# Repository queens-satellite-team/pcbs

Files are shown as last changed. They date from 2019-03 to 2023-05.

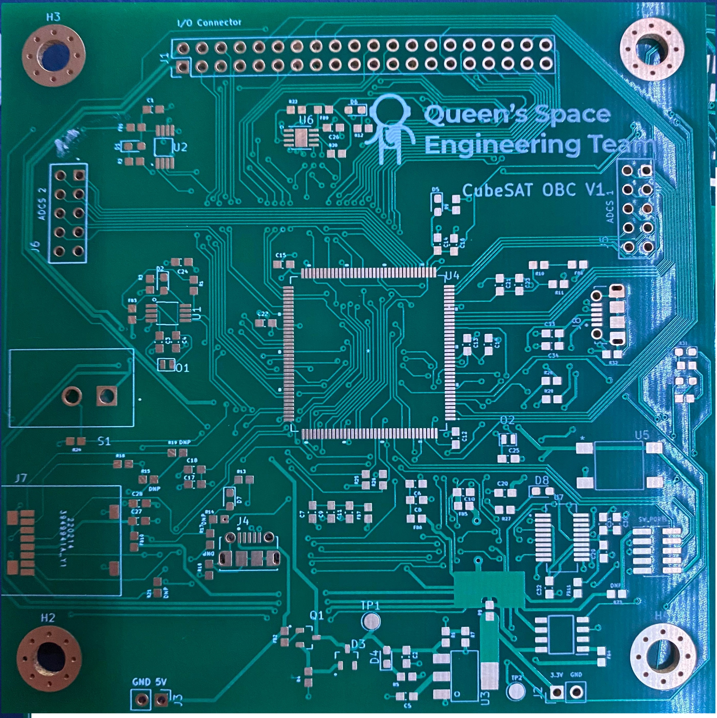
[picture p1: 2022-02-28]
OBC_Boards/STM32_Breakout/PCB_Frontside.jpg

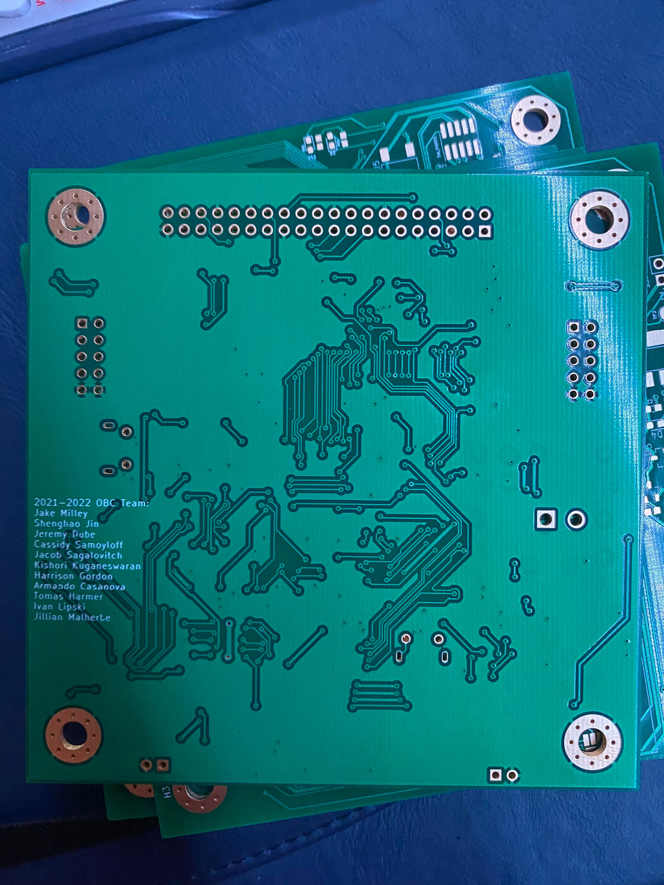
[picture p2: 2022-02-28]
OBC_Boards/STM32_Breakout/PCB_Backside.jpg

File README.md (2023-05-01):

# QSAT PCB Files

## Overview
This README contains information on how to setup your KiCad 6.0 environment. It includes:
1. How to use the existing schematic symbols and layout footprints
2. How to start a new project from an existing template
3. How to prepare the manufacturing and assembly files for ordering from JLCPCB

## Using QSAT PCB Symbols and Footprints

Following the instructions provided here: [How to Import into KiCad v6](https://support.snapeda.com/en/articles/5995733-how-to-import-into-kicad-v6-later)

**Import Symbols**

1. In KiCad, go to Preferences.

2. Click on Manage Symbol Libraries.

3. On the Global Libraries tab, click on Browse Libraries (the small folder icon below) 

4. Select the .lib file, then click Open. 

5. The library will appear, click OK.

6. Click on Symbol Editor.

7. Type on the filter search field, and navigate to the symbol you imported. Double-click over it to open the file.

**Import Footprints**

Using the *.kicad_mod file:

1. In KiCad, go to Preferences.

2. Click on Manage Footprint Libraries.

3. On the Global Libraries tab, click on Browse Libraries (the small folder icon below) 

4. Navigate to the Folder of the downloaded .kicad_mod file. Then click Select Folder. 

5. The library will appear, click OK. 

6. Click on Footprint Editor.

7. Type on the filter search field, and navigate to the footprint you imported. Double-click over it to open the file.

## Using QSAT PCB Templates

Following the instructions provided here: [KiCad Creating Templates](https://docs.kicad.org/5.1/en/kicad/kicad.html#creating_templates) we must:

1. Update our path configurations in KiCad to include the template folder.

a. Go to *Preferences* -> *Configure Paths* in the KiCad GUI.

b. Go to *KICAD_USER_TEMPLATE_DIR* and double click the path name until a folder apprears. 

c. Navigate to the *QSAT/pcbs/qsat-templates* directory and hit *Select Folder*

2. Create a new project from the template. 

a. Go to *File* -> *New Project From Template...* in the KiCad GUI.

b. Select the *User Templates* tab, and choose the template you want. 

**Note:** If starting a project from scratch it is recommended to use the *QSAT - PC104 Base Board* 
This is designed to have the same pcb footprint as the Clyde Space EPS board with mounting holes and
a PC104 connector.

## Ordering From JLCPCB

JLC has provided instructions for their required procedure, and is well detailed. 

The steps to generate the manufacturing files are found [here](https://support.jlcpcb.com/article/194-how-to-generate-gerber-and-drill-files-in-kicad-6). 

And the steps to generate the BOM and Centroid files are found [here](https://support.jlcpcb.com/article/84-how-to-generate-the-bom-and-centroid-file-from-kicad).

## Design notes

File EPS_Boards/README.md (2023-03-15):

EPS Printed Circuit Boards

**Note:** For the Solar Panel RevA, this file was made in KiCad 7.0 and can not be opened with earlier KiCad versions. 

|Board Name|Description|Status|Dinosaur Nickname|
|-|-|-|-|
|Solar Panel RevA| Supplies power generation capabilities for the satellite. Current PCB design is a smaller ~1U version to be used for testing. | Fabricated | TBD |
|Battery Board| Supplies power storage capabilites for the satellite. Contains voltage and current protections at the cell and system level. | In Progress | TBD |

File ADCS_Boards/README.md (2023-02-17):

# ADCS PCB Boards CSDC-6 (2022-2023)
We have three PCBs for ADCS. Their functionality is described below.

|Board Name|Description|Status|Dinosaur Nickname|
|-|-|-|-|
|Controller Board|The controller board houses the MCU and associated circuits, as well as the sun sensors.|In Progress|Irritator|
|Reaction Wheel Board|The RW-BD contains the reaction wheel driver boards and the IMUs.|In progress|Brachiosaurus|
|Magnetorquer Board|The MTQ-BD houses the magnetorquer coils and associated circuitry. If dedicated magnetometers are needed, they may be added to this board.|In Progress|Magyarosaurous|
|Photodiode Breakout Board|The photodiode board houses the photodiodes and is mounted to the solar panel boards|Completed|Ankylosaurus|

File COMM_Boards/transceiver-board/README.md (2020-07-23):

# QSAT transceiver-board 
This is the repo for the design of the tranciever for QSET's cube sattelite over 2018-2020
This may be made into a wiki, for now the readme works 

The following is a list of what is where: 

## Docs 
This folder contains the docs for the tranciver board meaning notes, and data sheets 
This is where the bill of materials and needs also live 
## Layout 
This has the KiCAD files for the tranciver layout

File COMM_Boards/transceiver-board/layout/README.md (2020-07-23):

# QSAT Tranciever Layout 
This part of the repo contains all of the KiCAD models 
Each version of the board is stored in a seperate folder with a version number

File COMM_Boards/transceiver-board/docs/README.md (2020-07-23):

# QSAT Tranceiver Document Storage 
This folder contains all documation and design notes, below is a listing of the sub dirs in this dir
## datasheets 
This subdir contains all of the data sheets for all of the componets 

#BOMs 
The boms will be saved with a version number and a rough date to ensure that it is sorta in the right date 
The boms are in the excel format 
The boms will utilize mutliple sheets to break it up a bit 
For the first version 
- one sheet is for the active devices like the ICs we are actually buying 
- one sheet is for passives 
- one sheet is for connecotrs

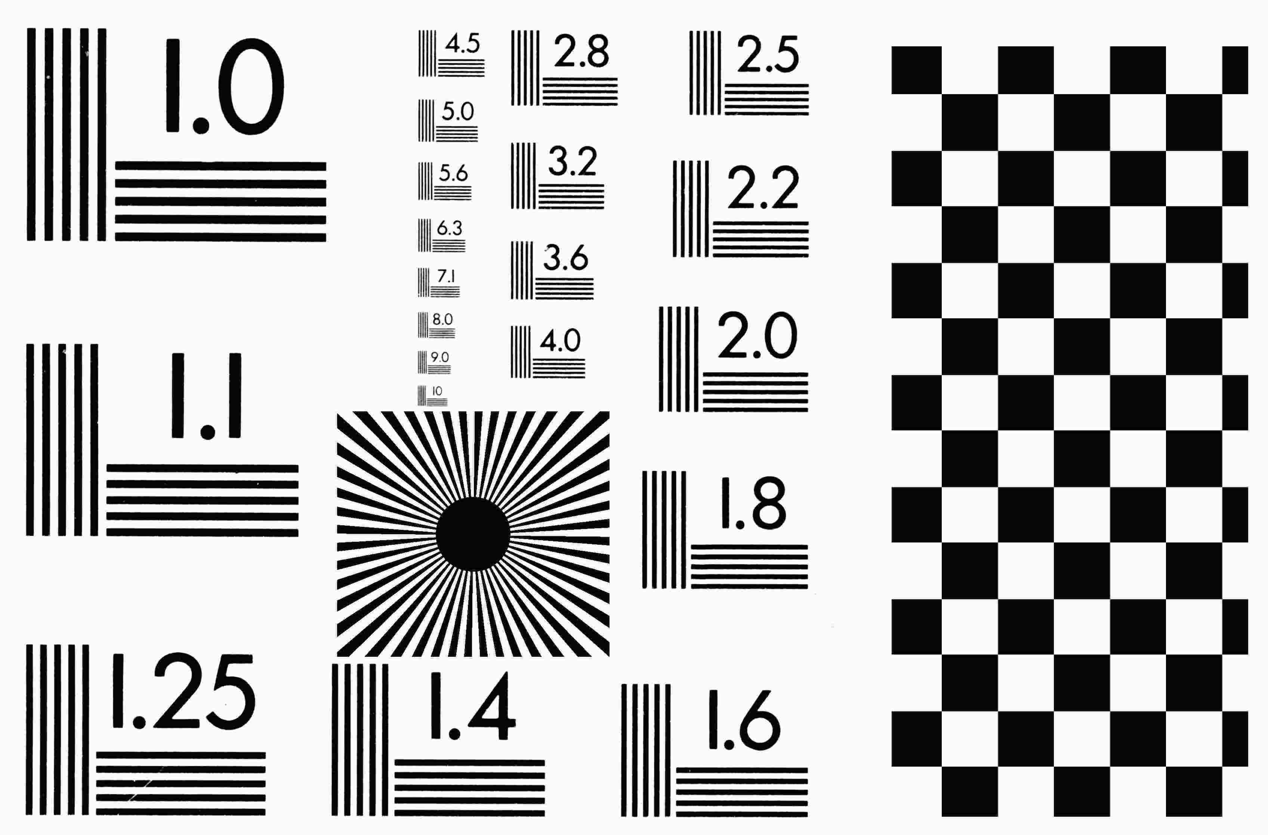
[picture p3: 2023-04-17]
qset-images/reschart.jpg

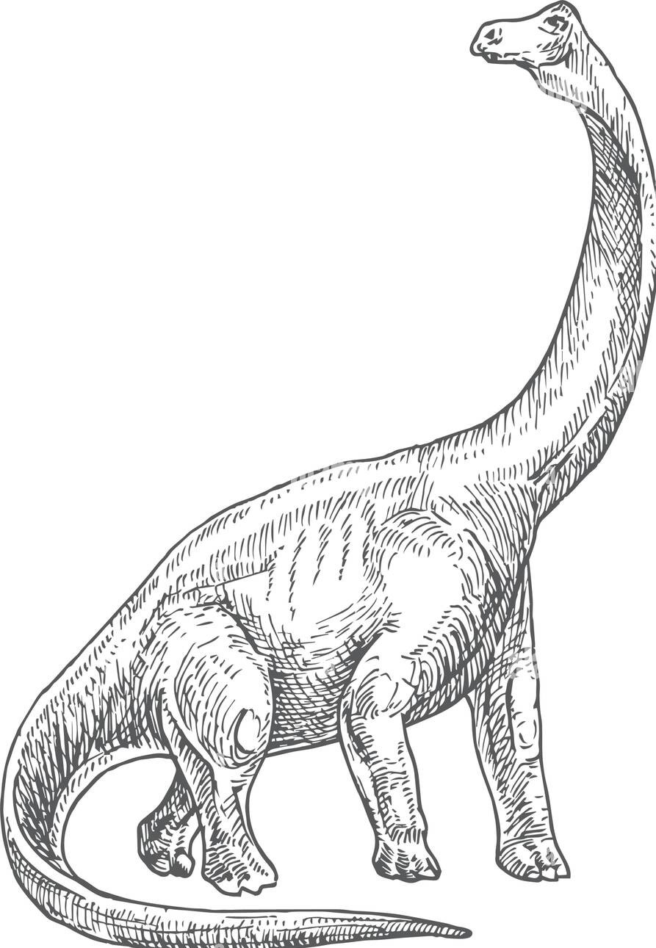
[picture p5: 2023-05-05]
qset-images/brontosaurus.jpg

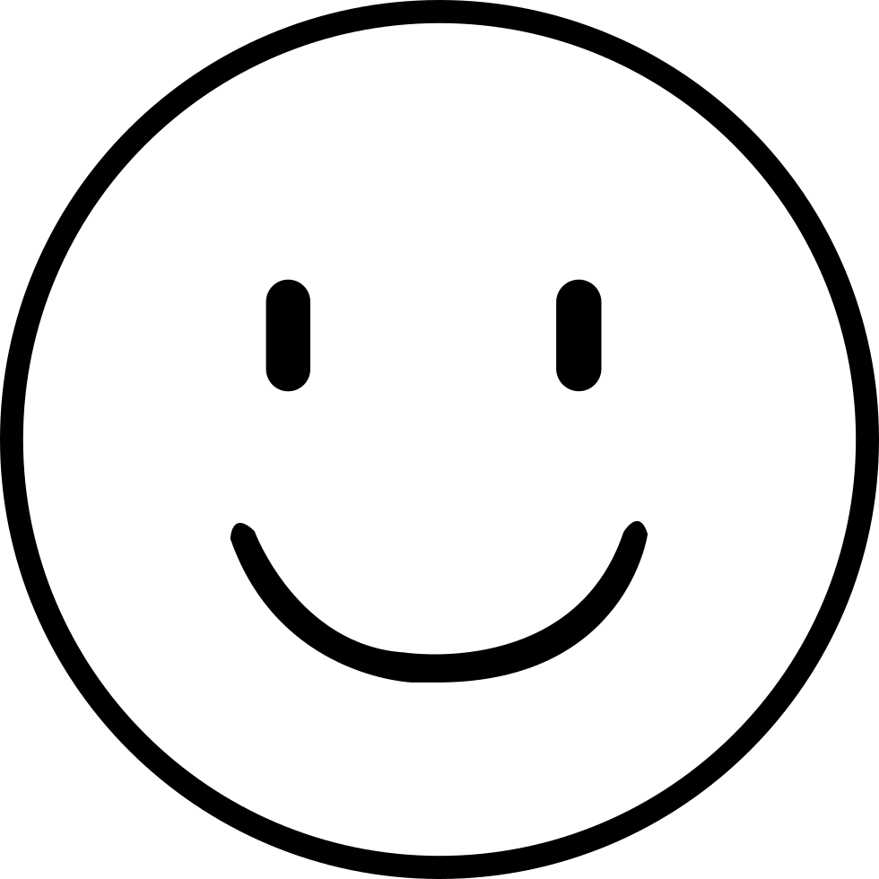
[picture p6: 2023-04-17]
qset-images/happy-face.png

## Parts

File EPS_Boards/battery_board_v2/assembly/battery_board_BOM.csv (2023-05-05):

Comment | Designator | Footprint | LCSC
0.1u | C1,C11,C20,C21 | Capacitor_SMD:C_0402_1005Metric | C361203
0.1u | C10,C14,C16,C17,C18,C19 | Capacitor_SMD:C_0603_1608Metric | C105907
0.1 uF | C13 | Capacitor_SMD:C_0402_1005Metric | C361203
10p | C2,C4 | Capacitor_SMD:C_0402_1005Metric | C382717
22n | C22 | Capacitor_SMD:C_0402_1005Metric | C301935
1nF | C24 | Capacitor_SMD:C_0402_1005Metric | C93920
0.1 uF | C25 | Capacitor_SMD:C_0603_1608Metric | C105907
22 uF | C26,C27,C28,C30,C31 | Capacitor_SMD:C_0603_1608Metric | C162690
10u | C3 | Capacitor_SMD:C_0402_1005Metric | C2992625
10u | C5 | Capacitor_SMD:C_0402_1005Metric | C2992625
100n | C6 | Capacitor_SMD:C_0402_1005Metric | C361203
10n | C7 | Capacitor_SMD:C_0402_1005Metric | C343046
22 uF | C8,C12,C15,C23,C29 | Capacitor_SMD:C_0402_1005Metric | C105226
1u | C9 | Capacitor_SMD:C_0402_1005Metric | C87145
100R @ 100 MHz | FB1 | Inductor_SMD:L_0603_1608Metric | C64181
100R @ 100MHz | FB2 | Inductor_SMD:L_0402_1005Metric | C2988088
2.2uH | L1,L2 | Inductor_SMD:L_0805_2012Metric_Pad1.15x1.40mm_HandSolder | C279882
100 | R1,R6 | Resistor_SMD:R_0402_1005Metric | C159942
910k | R10 | Resistor_SMD:R_0402_1005Metric | C137927
1M | R11,R14 | Resistor_SMD:R_0402_1005Metric | C131492
112k | R12 | Resistor_SMD:R_0402_1005Metric | C409664
1 M | R13,R24 | Resistor_SMD:R_0603_1608Metric | C2889400
681k | R15,R22 | Resistor_SMD:R_0402_1005Metric | C409718
280k | R16 | Resistor_SMD:R_0402_1005Metric | C364982
1 M | R17 | Resistor_SMD:R_0402_1005Metric | C131492
1M | R18 | Resistor_SMD:R_0603_1608Metric | C2889400
63.2k | R19 | Resistor_SMD:R_0603_1608Metric | C228003
10k | R2,R7,R9,R36 | Resistor_SMD:R_0402_1005Metric | C409612
560k | R20 | Resistor_SMD:R_0402_1005Metric | C162815
100k | R21 | Resistor_SMD:R_0402_1005Metric | C412435
240k | R23 | Resistor_SMD:R_0402_1005Metric | C352452
330 | R25,R26,R32,R33 | Resistor_SMD:R_0603_1608Metric | C103548
2.2k | R27,R28,R30,R31 | Resistor_SMD:R_0603_1608Metric | C103415
0.1 | R29 | Resistor_SMD:R_0603_1608Metric | C713432
1k | R37 | Resistor_SMD:R_0402_1005Metric | C279987
TMP36 | U1 | Package_SO:SOIC-8_3.9x4.9mm_P1.27mm | C691115
INA219AIDR | U12 | Package_SO:SOIC-8_3.9x4.9mm_P1.27mm | C138706
STM32F030F4P6 | U2 | Package_SO:TSSOP-20_4.4x6.5mm_P0.65mm | C32908
TPS63060 | U3,U7 | Package_SON:Texas_S-PWSON-N10_ThermalVias | C48567
74AUP1G08 | U6 | Package_TO_SOT_SMD:SOT-353_SC-70-5_Handsoldering | C507223
16 MHz | Y1 | Crystal:Crystal_SMD_3225-4Pin_3.2x2.5mm | C251610

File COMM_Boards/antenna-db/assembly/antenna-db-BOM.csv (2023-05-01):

Comment | Designator | Footprint | LCSC Part Number
0.1u | C1,C2,C3,C4 | Capacitor_SMD:C_0603_1608Metric | C105907
10u | C5,C6,C10 | Capacitor_SMD:C_0603_1608Metric | C466780
100n | C7,C8,C9,C11,C12 | Capacitor_SMD:C_0603_1608Metric | C105907
YLW | D1,D2 | LED_SMD:LED_0603_1608Metric | C2833057
100R @ 100M | FB1 | Inductor_SMD:L_0603_1608Metric | C142080
10k | R13 | Resistor_SMD:R_0603_1608Metric | C217281
0 | R2,R4 | Resistor_SMD:R_0603_1608Metric_Pad0.98x0.95mm_HandSolder | C881308
100k | R5,R7 | Resistor_SMD:R_0603_1608Metric | C217279
2k2 | R6,R8 | Resistor_SMD:R_0603_1608Metric | C2889375
0 | R9,R10,R11,R12 | Resistor_SMD:R_0603_1608Metric | C881308
STM32F030CCT6 | U5 | QFP50P900X900X160-48N | C81787

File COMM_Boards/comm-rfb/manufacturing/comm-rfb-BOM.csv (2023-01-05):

Comment | Designator | Footprint | LCSC Part Number
0.1uF | C11 | Capacitor_SMD:C_0603_1608Metric | C105907
100n | C12,C13,C14,C19,C99 | Capacitor_SMD:C_0603_1608Metric | C105907
10n | C15 | Capacitor_SMD:C_0603_1608Metric | C385970
1u | C16,C17 | Capacitor_SMD:C_0603_1608Metric | C167338
10u | C18 | Capacitor_SMD:C_0603_1608Metric | C91150
20p | C2 | Capacitor_SMD:C_0402_1005Metric | C107000
22u | C20,C21 | Capacitor_SMD:C_0603_1608Metric | C87153
1000p | C3,C4,C5 | Capacitor_SMD:C_0402_1005Metric | C106205
10p | C6,C7 | Capacitor_SMD:C_0402_1005Metric | C650948
1p8 | C8 | Capacitor_SMD:C_0402_1005Metric | C76903
10p | C9,C10 | Capacitor_SMD:C_0603_1608Metric | C56033
LED BLUE | D1 | LED_SMD:LED_0603_1608Metric | C2837377
LED BLUE | D3 | Diode_SMD:D_0603_1608Metric | C2837377
100R @ 100 MHz | FB1 | Inductor_SMD:L_0603_1608Metric | C96995
100R @ 100MHz | FB2 | Inductor_SMD:L_0603_1608Metric | C96995
Conn_Coaxial | J6,J7 | Connector_Coaxial:U.FL_Hirose_U.FL-R-SMT-1_Vertical | C88373
Conn_Coaxial | J8,J9 | Connector_Coaxial:SMA_Amphenol_132134-11_Vertical | C2693814
150n | L1 | Inductor_SMD:L_0402_1005Metric | C162548
22n | L2 | Inductor_SMD:L_0402_1005Metric | C142243
12n | L3 | Inductor_SMD:L_0402_1005Metric | C86128
9.1k | R1 | Resistor_SMD:R_0603_1608Metric | C101399
10k | R10 | Resistor_SMD:R_0603_1608Metric | C269701
330 | R2 | Resistor_SMD:R_0402_1005Metric | C156103
15 | R3 | Resistor_SMD:R_0402_1005Metric | C208806
1k5 | R4 | Resistor_SMD:R_0603_1608Metric | C114668
100m | R5 | Resistor_SMD:R_0402_1005Metric | C724023
2.2k | R9 | Resistor_SMD:R_0603_1608Metric | C116387
STM32F030CCT6 | U1 | qset-footprints:QFP50P900X900X160-48N | C81787
AMS1117-3.3 | U3 | Package_TO_SOT_SMD:SOT-223-3_TabPin2 | C110474
16 MHz | Y1 | Crystal:Crystal_SMD_3225-4Pin_3.2x2.5mm | C251610

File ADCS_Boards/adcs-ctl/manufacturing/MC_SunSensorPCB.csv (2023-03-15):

Comment | Designator | Footprint | LCSC | Link
100nF | C1,C17,C22,C23,C24,C43 | Capacitor_SMD:C_0603_1608Metric | C91183 | https://jlcpcb.com/partdetail/Yageo-CC0603JRX7R9BB104/C91183
4pF | C10,C13 | Capacitor_SMD:C_0402_1005Metric | C458866 | https://jlcpcb.com/partdetail/Walsin_TechCorp-0402N4R0B500CT/C458866
10nF | C11 | Capacitor_SMD:C_0402_1005Metric | C386111 | https://jlcpcb.com/partdetail/TaiyoYuden-UMK105B7103KVHF/C386111
1uF | C12,C14 | Capacitor_SMD:C_0603_1608Metric | C458914 | https://jlcpcb.com/partdetail/Walsin_TechCorp-0603X105J6R3CT/C458914
1.0uF | C15,C37,C38 | Capacitor_SMD:C_0603_1608Metric | C458914 | https://jlcpcb.com/partdetail/Walsin_TechCorp-0603X105J6R3CT/C458914
180pF | C18,C19,C20,C21,C25,C26,C27,C28,C29,C30,C31,C32,C33,C34,C35,C36 | Capacitor_SMD:C_0603_1608Metric | C107041 | https://jlcpcb.com/partdetail/Yageo-CC0603JRNPO9BN181/C107041
10uF | C2,C6,C9,C16 | Capacitor_SMD:C_0603_1608Metric | C19702 | https://jlcpcb.com/partdetail/20411-CL10A106KP8NNNC/C19702
100nF | C3,C4,C5,C7,C8 | Capacitor_SMD:C_0402_1005Metric | C361203 | https://jlcpcb.com/partdetail/Tdk-C1005X5R1E104KT000E/C361203
0.1uF | C39,C40,C41,C42 | Capacitor_SMD:C_0603_1608Metric | C91183 | https://jlcpcb.com/partdetail/Yageo-CC0603JRX7R9BB104/C91183
GREEN_LED | D1,D2,D3 | LED_SMD:LED_0603_1608Metric | C165981 | https://jlcpcb.com/partdetail/177364-BL_HKC36G_AVTRB/C165981
FerriteBead | FB1 | Inductor_SMD:L_0603_1608Metric | C2661871 | https://jlcpcb.com/parts/componentSearch?searchTxt=C2661871
100R @ 100 MHz | FB2 | Inductor_SMD:L_0603_1608Metric | C2661871 | https://jlcpcb.com/parts/componentSearch?searchTxt=C2661871
RE1C002UNTCL | Q1,Q2 | qset-footprints:RE1C002UNTCL | C509959 | https://jlcpcb.com/partdetail/RohmSemicon-RE1C002UNTCL/C509959
10k | R1 | Resistor_SMD:R_0603_1608Metric | C374378 | https://jlcpcb.com/partdetail/VikingTech-AR03ATC1002A/C374378
2.2k | R10,R11,R24,R25 | Resistor_SMD:R_0603_1608Metric | C186194 | https://jlcpcb.com/partdetail/Koa_SpeerElec-RN73H1JTTD2201B25/C186194
2k2 | R2,R26 | Resistor_SMD:R_0603_1608Metric | C186194 | https://jlcpcb.com/partdetail/Koa_SpeerElec-RN73H1JTTD2201B25/C186194
10k | R27,R28 | Resistor_SMD:R_0402_1005Metric | C406733 | https://jlcpcb.com/partdetail/VikingTech-CR_02FL6_10K/C406733
1Meg | R3 | Resistor_SMD:R_0603_1608Metric | C335092 | https://jlcpcb.com/partdetail/VikingTech-ARG03BTC1004/C335092
2Meg | R4 | Resistor_SMD:R_0603_1608Metric | C22976 | https://jlcpcb.com/partdetail/23703-0603WAF2004T5E/C22976
1k | R5 | Resistor_SMD:R_0603_1608Metric | C217840 | https://jlcpcb.com/partdetail/VikingTech-ARG03FTC1001/C217840
5.76k | R6,R7,R8,R9,R12,R13,R14,R15,R16,R17,R18,R19,R20,R21,R22,R23 | Resistor_SMD:R_0603_1608Metric | C218094 | https://jlcpcb.com/partdetail/VikingTech-ARG03FTC5761/C218094
TL3305CF260QG | S1 | SW_TL3305CF260QG | C2886904 | https://jlcpcb.com/partdetail/eswitch-TL3305CF260QG/C2886904
STM32F103RET6 | U1 | QFP50P1200X1200X160-64N | C8322 | https://jlcpcb.com/partdetail/Stmicroelectronics-STM32F103RET6/C8322
MR25H10MDF | U16 | SON65P300X300X95-8N | C246235 | https://jlcpcb.com/partdetail/EverspinTech-MR25H40CDF/C246235
AMS1117-3.3 | U2 | Package_TO_SOT_SMD:SOT-223-3_TabPin2 | C369933 | https://jlcpcb.com/partdetail/Kexin-AMS1117_33/C369933
AMS1117-1.8 | U3 | Package_TO_SOT_SMD:SOT-223-3_TabPin2 | C489389 | https://jlcpcb.com/partdetail/Kexin-AMS1117_18/C489389
LM358N | U4 | DIP794W45P254L959H508Q8 | C434570 | https://jlcpcb.com/partdetail/Hgsemi-LM358N/C434570
CD74HC4067M96 | U5 | SOIC127P1030X265-24N | C496123 | https://jlcpcb.com/partdetail/TexasInstruments-CD74HC4067M96/C496123
LM324N | U6,U7,U8,U9 | qset-footprints:Op-Amp | C725320 | https://jlcpcb.com/partdetail/Hgsemi-LM324N/C725320
Crystal_GND24 | Y1 | Crystal:Crystal_SMD_3225-4Pin_3.2x2.5mm | C251610 | https://jlcpcb.com/partdetail/247413-7U16000E12UCG/C251610
9DoF IMU | U1, U3 | QFN-24(3x3) | C726001 | https://jlcpcb.com/partdetail/TdkInvensense-ICM20948/C726001 | THIS PART IS NOT IN STOCK | https://www.mouser.ca/ProductDetail/TDK-InvenSense/ICM-20948?qs=u4fy%2FsgLU9OtGc31yF%2Friw%3D%3D

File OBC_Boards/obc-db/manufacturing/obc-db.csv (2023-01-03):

Comment | Designator | Footprint | LCSC
BHSD-2032-SM | BT1 | qset-footprints:BAT_BHSD-2032-SM | N/A
22uF | C1,C2 | Capacitor_SMD:C_0603_1608Metric | C71001
100nF | C4,C8 | Capacitor_SMD:C_0603_1608Metric | C116838
18pF | C5,C6 | Capacitor_SMD:C_0603_1608Metric | C363547
10uF | C3,C7 | Capacitor_SMD:C_0603_1608Metric | C386081
LED | D1,D2,D3,D6,D7 | LED_SMD:LED_0603_1608Metric | C389517
DIODE | D4,D5 | Diode_SMD:D_0603_1608Metric | C2463
100R @ 100 MHz | FB1,FB3,FB4,FB5 | Inductor_SMD:L_0603_1608Metric | C64181
Raspberry Pi 4 Connector | J2 | Connector_PinSocket_2.54mm:PinSocket_2x20_P2.54mm_Vertical | N/A
10k | R1,R2,R3,R7 | Resistor_SMD:R_0603_1608Metric | C216802
2.2k | R4,R5,R9,R11,R12 | Resistor_SMD:R_0603_1608Metric | C114662
20k | R6 | Resistor_SMD:R_0603_1608Metric | C365117
100m | R8 | Resistor_SMD:R_0402_1005Metric | C724023
L102021MS02Q | U1 | L102021MS02Q | N/A
AZ1117IH-3.3TRG1 | U2 | Package_TO_SOT_SMD:SOT-223-3_TabPin2 | C110474
MCP3008-I/SL | U3 | 16-SOIC | C1520159
MAX4372FESA+ | U4 | (8-SOIC (0.154", 3.90mm Width)) | C1346175
MCP79400T-I/SN | U5 | MCP79400T (8-SOIC) | C623881
MCP9808T-E/MC | U6 | MCP9808T-E&slash_MC | C9900034299
MR01A-01211 | U7 | SMD:MR01A-01211 | C479742
CM9V-T1A | Y1 | XTAL_CM9V-T1A-32.768KHZ-9PF-20PPM-TA-QC | N/A

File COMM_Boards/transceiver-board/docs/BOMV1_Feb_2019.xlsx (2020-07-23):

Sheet: ActiveStuff
Part Name | Part Number and Link | Vendor | Unit Cost (CAD) | Quantity | Total | Notes
RF Tranciever | MKW01Z128CHN-ND (https://www.digikey.ca/product-detail/en/nxp-usa-inc/MKW01Z128CHN/MKW01Z128CHN-ND/4746295) | Digikey | 10.37 | 5 | 51.85
32 Mhz Crysal Res | SER3801CT-ND (https://www.digikey.ca/product-detail/en/epson/FA-20H-32.0000MF20X-K3/SER3801CT-ND/3198123) | Digikey | 0.71 | 5 | 3.55

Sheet: Passives
Shcematic Number | Type | Size | Part Number and Link | Vendor | Unit Cost (CAD) | Quantity | Total | Notes

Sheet: Connectors
Part Name | Part Number and Link | Vendor | Unit Cost (CAD) | Quantity | Total | Notes
SMA Connector | J502-NDhttps://www.digikey.ca/product-detail/en/cinch-connectivity-solutions-johnson/142-0701-801/J502-ND/35280 | Digikey | 5.29 | 2 | 10.58 | Get as many as you want, these are pretty robust and can survive many solder-desolder cycles if you are carful
SMA 50 Ohm Load | WM9473-NDhttps://www.digikey.ca/product-detail/en/molex/0733910680/WM9473-ND/3878259 | Digikey | 6.88 | 2 | 13.76 | Assuming we make a test Tx and Rx

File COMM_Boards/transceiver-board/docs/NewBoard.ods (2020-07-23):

Schematic Name | Name | Part Number | Link | Vendor | Unit Cost | Units | Total | Notes
 | High power radio | 1783-1050-1-ND | https://www.digikey.ca/product-detail/en/radiocrafts-as/RC1740HP-RC232/1783-1050-1-ND/7100652 | digikey | 61.31 | 1 |  | 27 dBm
 | Low Power Radio | 1783-1031-1-ND | https://www.digikey.ca/product-detail/en/radiocrafts-as/RC1140-RC232/1783-1031-1-ND/7100633 | digikey | 19.74 | 1 |  | 10 dBm
R7 and R8 | 150 Ohm 0603 Resistor | P15KDBCT-ND | https://www.digikey.ca/product-detail/en/panasonic-electronic-components/ERA-3AEB153V/P15KDBCT-ND/1466080 | digikey | 0.53 | 2
R1 | 2.7 K 603 Ressitor | P2.7KDBCT-ND | https://www.digikey.ca/product-detail/en/panasonic-electronic-components/ERA-3AEB272V/P2.7KDBCT-ND/1466062 | digikey | 0.53 | 1
C1 | 1nF Cap | 1284-1177-1-ND | https://www.digikey.ca/product-detail/en/american-technical-ceramics/600S1R0AT250XT/1284-1177-1-ND/3905517 | digikey | 1.7 | 1
R2 | 8.2 k R 0603 | RR08P8.2KDDKR-ND | https://www.digikey.ca/product-detail/en/susumu/RR0816P-822-D/RR08P8.2KDDKR-ND/580112 | digikey | 0.17 | 1
R3 | 5.6k R 0603 | RR08P5.6KDDKR-ND | https://www.digikey.ca/product-detail/en/susumu/RR0816P-562-D/RR08P5.6KDDKR-ND/580093 | digikey | 0.17 | 1
R4 | short | RMCF0603ZT0R00CT-ND | https://www.digikey.ca/product-detail/en/stackpole-electronics-inc/RMCF0603ZT0R00/RMCF0603ZT0R00CT-ND/1943218 | digikey | 0.15 | 1
L1 | Choke | 490-3997-1-ND | https://www.digikey.ca/product-detail/en/murata-electronics-north-america/BLM18SG331TN1D/490-3997-1-ND/1016257 | digikey | 0.2 | 1
 | LED | SML-D12U1WT86CT-ND | https://www.digikey.ca/product-detail/en/rohm-semiconductor/SML-D12U1WT86/SML-D12U1WT86CT-ND/5843858 | digikey | 0.31 | 2

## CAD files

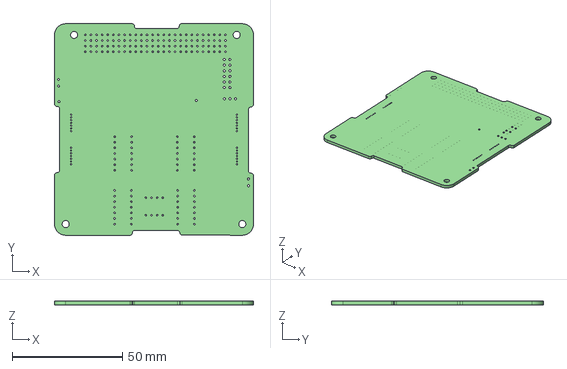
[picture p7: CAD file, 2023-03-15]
ADCS_Boards/adcs-ctl/adcs-ctl.step
90.2 x 95.9 x 1.61 mm

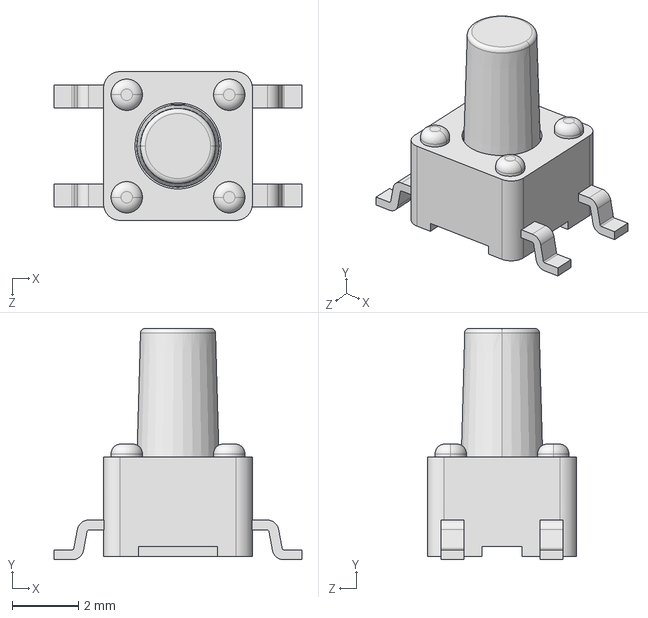
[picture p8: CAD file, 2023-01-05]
ADCS_Boards/adcs-ctl/Symbols/TL3305CF260QG.step
7.50 x 7.00 x 4.50 mm

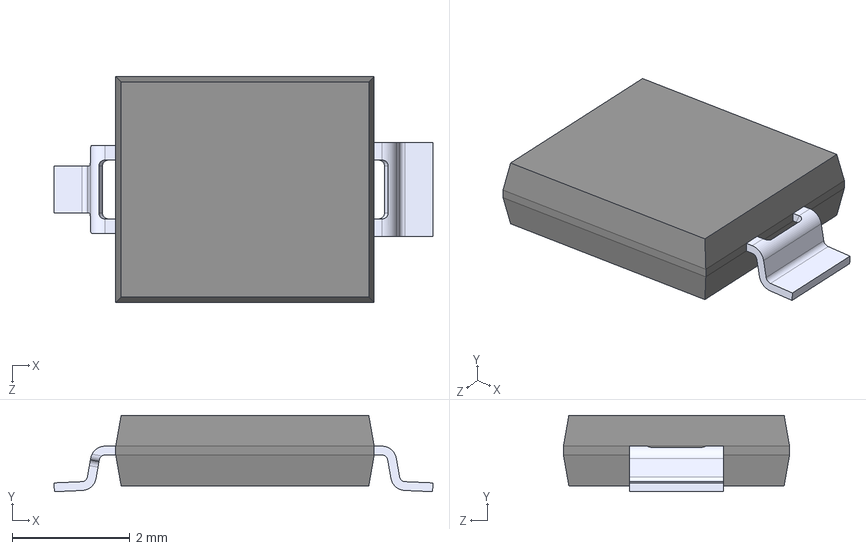
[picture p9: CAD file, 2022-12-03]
ADCS_Boards/ptd-db/SFH_2430-Z/SFH_2430-Z.step
6.45 x 1.30 x 3.85 mm

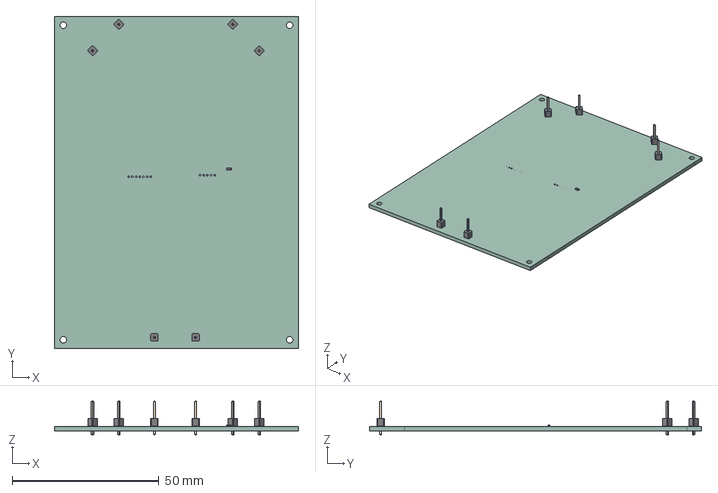
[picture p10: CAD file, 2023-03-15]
EPS_Boards/solar_panel_v1/solar_panel_v1.step
83.0 x 113.0 x 11.5 mm
PCB

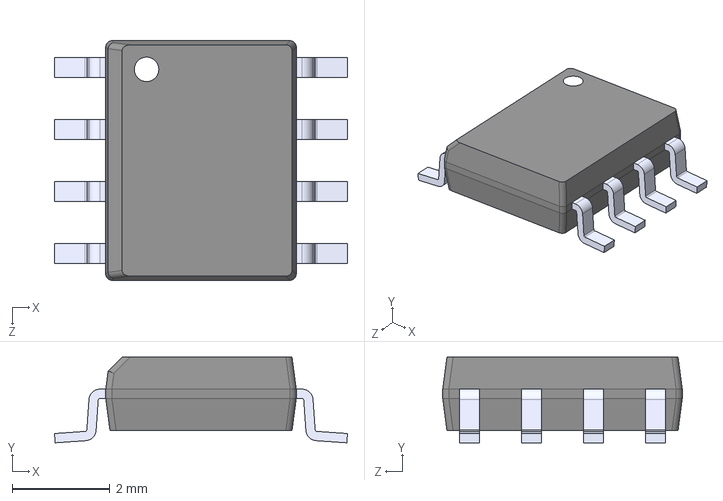
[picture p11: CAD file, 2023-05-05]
qset-libraries/qset-step-files/UCC2946D.step
5.99 x 1.75 x 4.90 mm

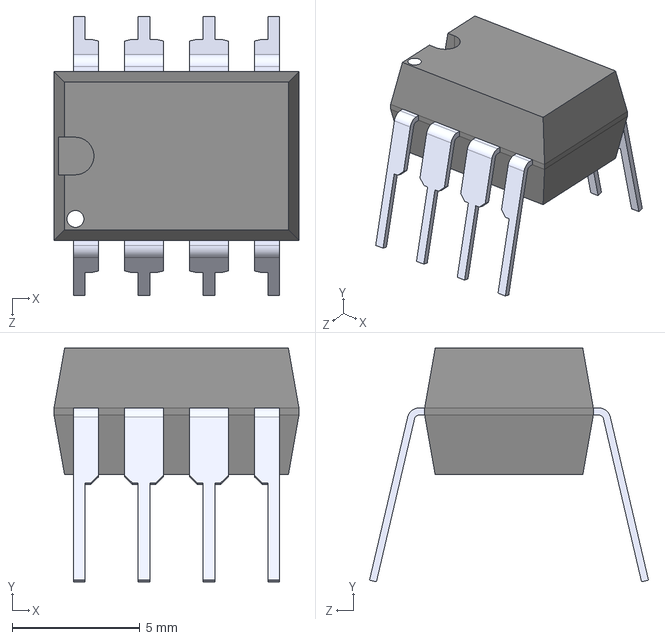
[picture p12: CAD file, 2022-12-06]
qset-libraries/qset-symbols/LM358N_NOPB.step
9.59 x 9.14 x 10.9 mm

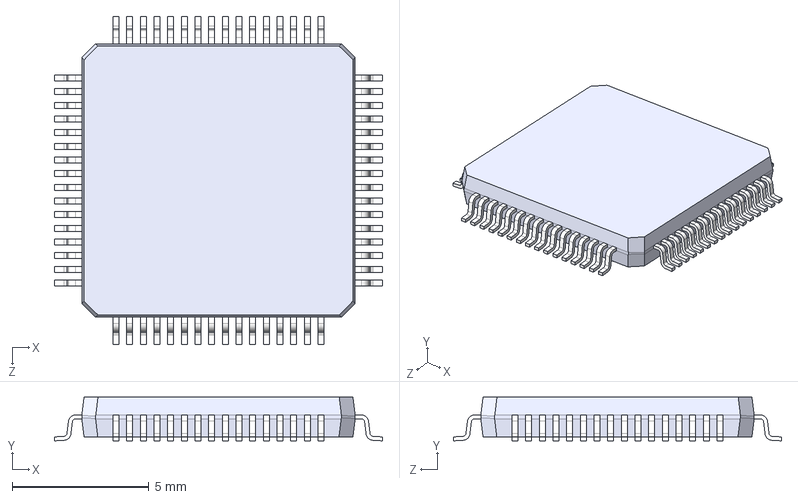
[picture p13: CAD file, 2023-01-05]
ADCS_Boards/adcs-ctl/Symbols/STM32F103RET6.step
12.0 x 1.60 x 12.0 mm

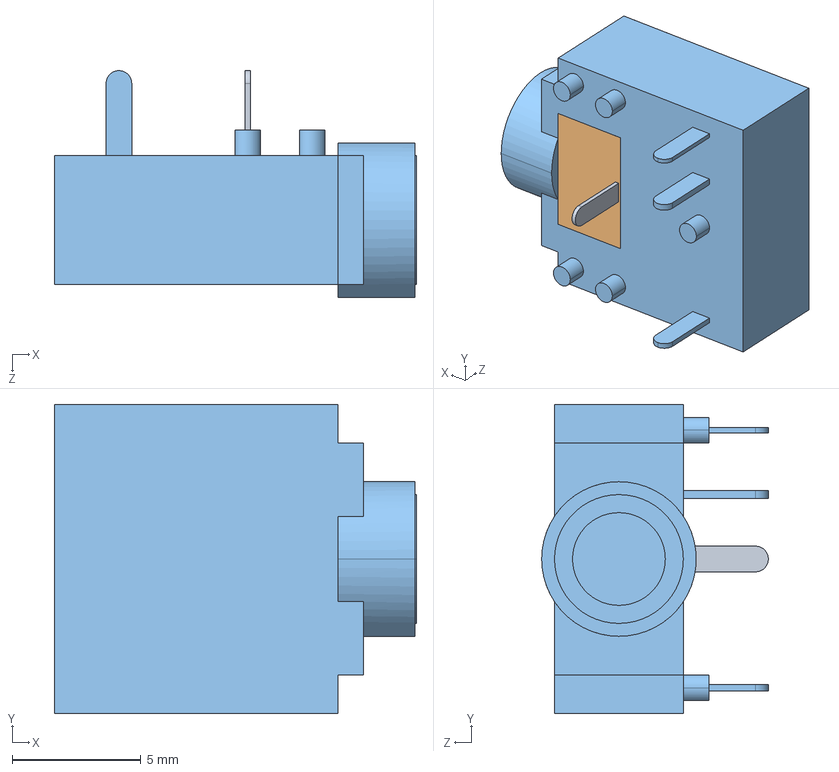
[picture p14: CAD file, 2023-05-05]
qset-libraries/qset-step-files/CUI_DEVICES_SJ1-3524NG.step
14.0 x 12.0 x 8.80 mm

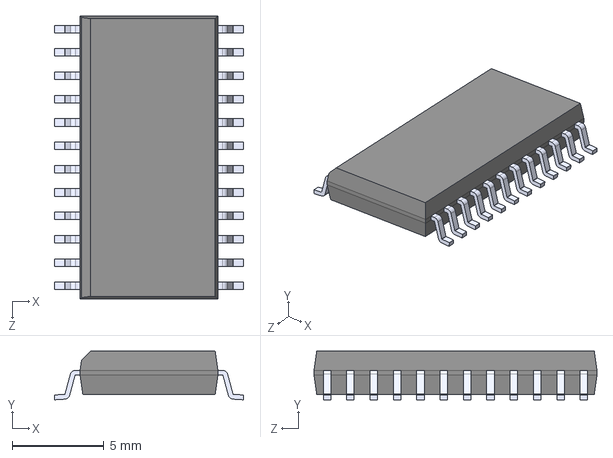
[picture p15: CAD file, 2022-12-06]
qset-libraries/qset-symbols/CD74HC4067M96.step
10.3 x 2.65 x 15.4 mm

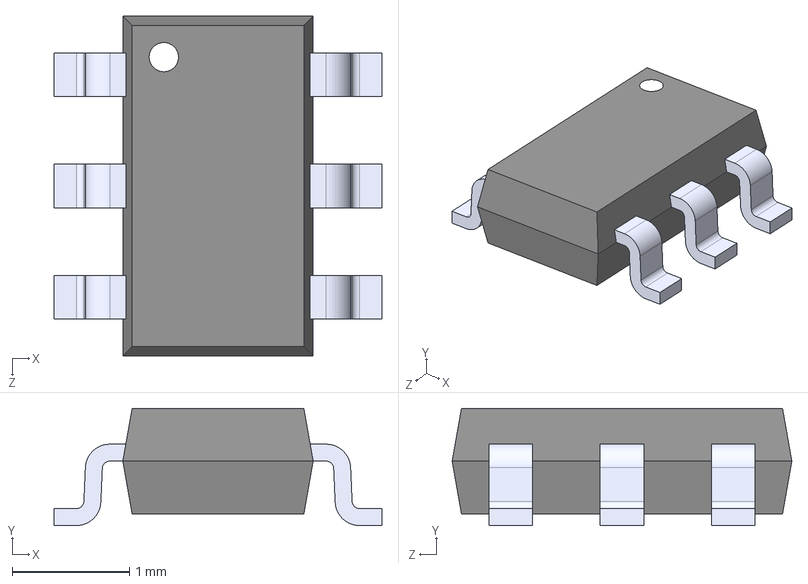
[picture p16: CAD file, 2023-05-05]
qset-libraries/qset-step-files/LTC6995HS6-1_TRMPBF.step
2.80 x 1.00 x 2.90 mm

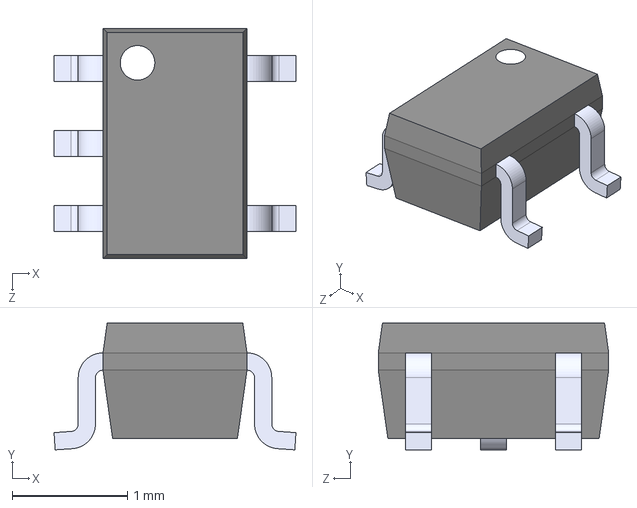
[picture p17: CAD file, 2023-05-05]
qset-libraries/qset-step-files/SOT65P210X110-5N.step
2.10 x 1.10 x 2.00 mm

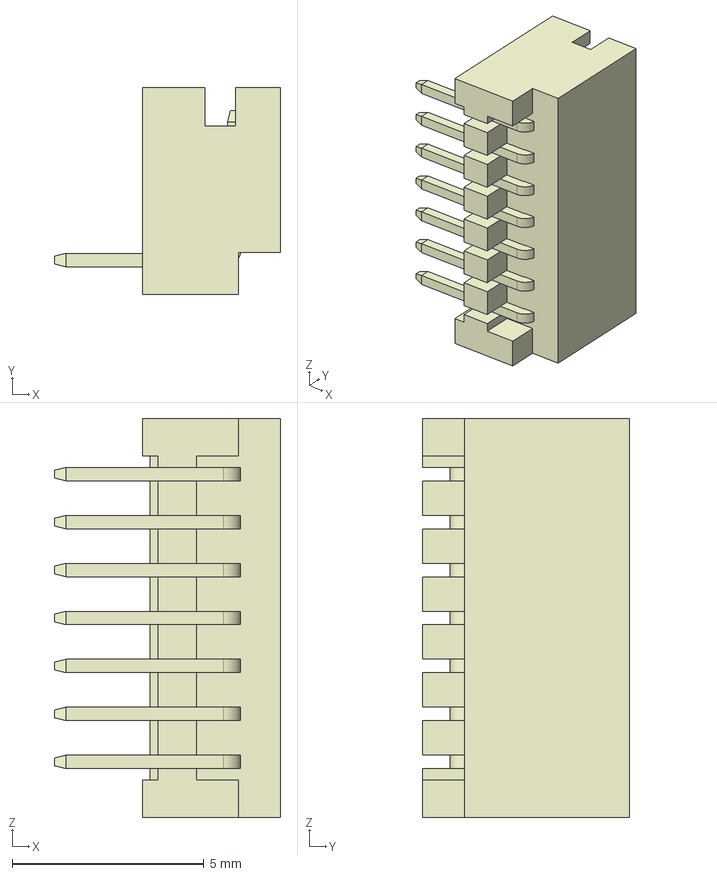
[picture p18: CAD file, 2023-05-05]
qset-libraries/qset-step-files/DF13-7P-1.25DS.stp
5.90 x 5.40 x 10.4 mm

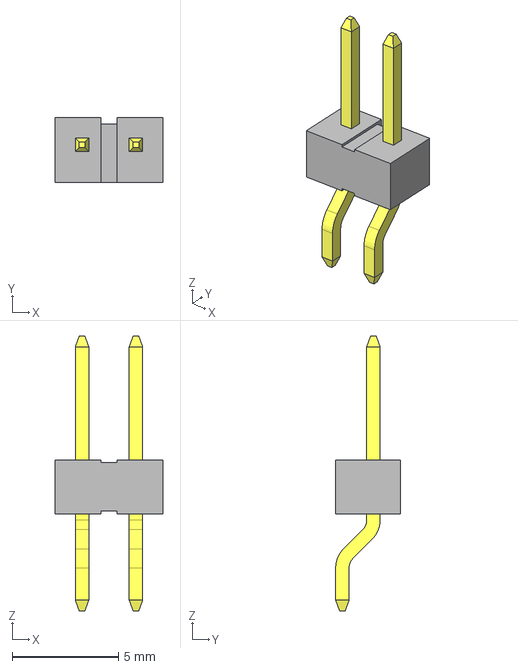
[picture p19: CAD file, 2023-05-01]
qset-libraries/qset-step-files/TSM-102-01-L-SH.step
5.08 x 3.05 x 13.0 mm
T-1S6-08(-01-2-SH)
TSM-102-01-SH_body

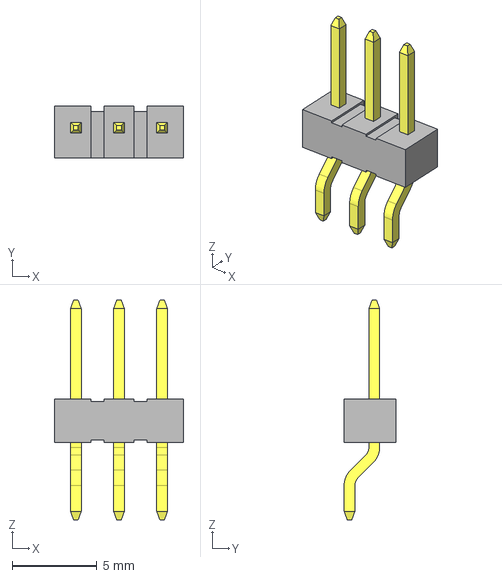
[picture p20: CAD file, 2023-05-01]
qset-libraries/qset-step-files/TSM-103-01-L-SH.step
7.62 x 3.05 x 13.0 mm
T-1S6-08(-01-3-SH)
TSM-103-01-SH_body

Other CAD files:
ADCS_Boards/adcs-ctl/Symbols/LM358N_NOPB.step
qset-libraries/qset-step-files/SFH_2430-Z.step
ADCS_Boards/adcs-ctl/Symbols/CD74HC4067M96.step
qset-libraries/qset-step-files/TSM-104-01-L-SH.step
ADCS_Boards/adcs-ctl/Symbols/1825232-1.step
qset-libraries/qset-step-files/1-1734248-1-reaction-wheel-connector.stp
qset-libraries/qset-step-files/BHSD-2032-SM--3DModel-STEP-1.STEP
qset-libraries/qset-step-files/CM9V-T1A-32.768KHZ-9PF-20PPM-TA-QC.STEP
qset-libraries/qset-step-files/DFN8_2x3MC_MCH.step
qset-libraries/qset-step-files/L102021MS02Q.stp
qset-libraries/qset-step-files/MAX4372FESA+.STEP
qset-libraries/qset-step-files/MS.STEP
qset-libraries/qset-step-files/RE1C002UNTCL.step
qset-libraries/qset-step-files/SOIC16-N_MC_MCH.step
qset-libraries/qset-step-files/STM32F030CCT6.step
qset-libraries/qset-step-files/TFM-110-02-SM-D-A-K-TR.step
qset-libraries/qset-step-files/TFM-110-02-SM-D-A-K-TR.stp
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

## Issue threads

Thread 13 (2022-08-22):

OBC-DB: NOR Flash Chip

jillianmalherbe, 2022-08-22:
### Template Issue To-Do List
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

# Motivation ⛰️
> Provide a short description of the issue and explain why it is required to work on this issue.

# Next Steps 🚶
> Provide a list of steps for someone to complete in order to finish the issue.

- [ ] this is step one
- [ ] this is step two
- [ ] this is step three

# Supporting Material and Resources 📖
> If any links, resources, or past work would be useful include the links here

- [Markdown Style Guide for Creating Issues](https://www.markdownguide.org/basic-syntax/)

# Definition of Done 💯
> Be specific. There should be a concrete change that occurs after this issue is closed. Something is simplified, created, modified, replaced, enhanced, etc.

### Tags
> tag people that should know about this issue

SeanTedesco, 2023-05-23:
The team decided against using NOR flash as an external memory source as it was deemed an unnecessary additional complexity. Closing issue.

Closed 2023-05-23.

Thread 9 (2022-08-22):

Umbillical Debug Interface Board

jillianmalherbe, 2022-08-22:
# Motivation ⛰️
> We need a way to plug into the OBC and get status updates without needing to disassemble the Selfie-Sat. Thus, the team will be designing and assembling an additional custom PCB which we will call the Umbilical Debug Interface Board (OBC-IB). This board will be populated with ports and LED's and will also contain some ports that will be routed directly to the EPS subsystem (such as a battery charging port). The idea is to eventually have this board positioned parallel to the outer wall of the satellite with the LED light exposed and we want the front of the ports to be flush with the outer wall of the CubeSat. Certain components such as the Ethernet Interface will be routed directly to the Rpi-4 ethernet port while others will be routed to the daughterboard through a connector.
> We want to have all of the components selected before CDR (October 24th) so that we can include our preliminary design in the presentation. It might also be nice to have an initial layout for the board completed for the presentation but we'll see how things progress.

# Next Steps 🚶

- [ ] Read through the requirements needed for this project which can be found in the OBC design document under 6.4.3 "Umbilical Debugging Interface Board"
- [ ] Research ports and components that would be good to have on the board based on the listed requirements. Make a list of these components.
- [ ] Communicate with the mech team, specifically @TyeD to discuss dimensions for the board and where it will be located on the Selfie Sat.
- [ ] Create a KiCad schematic file for the PCB in the pcbs repository. (Ask @jillianmalherbe or @sirlipski for help if you're unsure)
- [ ] Insert the symbols and footprints for the selected components into the KiCad schematic. The board must also include a PMOD connector which will be routed to the OBC Daughterboard.
- [ ] In KiCad, make the PCB the correct dimensions that were decided upon with the mech team. Complete the layout for the PCB by dragging components onto the CAD board and drawing the appropriately sized traces between components, LED's and connectors. (We will have a tutorial on this when the time comes)
- [ ] Present the board to the team during one of our OBC Design Reviews, get feedback and iterate upon the design.

# Supporting Material and Resources 📖

- This project mostly involves using KiCad and there are many tutorials online which can be helpful. This playlist in particular is very helpful if you're completely new to the software : https://www.youtube.com/watch?v=vaCVh2SAZY4&list=PL3bNyZYHcRSUhUXUt51W6nKvxx2ORvUQB

# Definition of Done 💯
- All requirements for this PCB outlined in the OBC design document have been satisfied.
- All components have been selected and links to all components can be found in the project's BOM.
- Brief descriptions explaining why certain components were selected can be found in the OBC design document.
- A schematic file has been completed for the design.
- An initial PCB layout has been completed.

### Tags
@jillianmalherbe @SeanTedesco @emmapaczkowski

SeanTedesco, 2023-05-23:
Board has been made and is in use. Closing issue.

Closed 2023-05-23.

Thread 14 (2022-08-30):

Development: PC104 Breakout Board

SeanTedesco, 2022-08-30:
# Motivation ⛰️
The team is using the PC104 standard for all of its PCB designs. Since we are always wanting to test and develop new sub-systems, having a protoboard or breakout board that can easily integrate with the rest of the system would be beneficial.

# Next Steps 🚶
- [ ] confirm pinout with Clyde Space EPS pin out
- [ ] make a draft layout of all the through holes and their usage
- [ ] perform routing and layout of PCB using KiCad PC104 template
- [ ] make BOM
- [ ] order PCB and parts
- [ ] assemble and test connections on PCB

# Supporting Material and Resources 📖
[Pumpkin Space](https://www.pumpkinspace.com/store/p50/Protoboard_Module_Kit.html) offers a protoboard with the following description: "The Protoboard Module Kit provides an easy way to wire through-hole components into circuitry that connects to the CubeSat Kit Bus Connector. An 0.100" grid with roughly 500 plated holes is provided for mounting and interconnecting through-hole components. Power buses on each side for +5V_SYS, VCC_SYS and GND are provided." The protoboard is shown below.

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

# Definition of Done 💯
- PCBs are now used for testing

### Tags

cc: @SeanTedesco

Closed 2022-12-16.

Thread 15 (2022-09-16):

OBC-DB: Temperature Sensor Circuit Development

jillianmalherbe, 2022-09-16:
# Motivation ⛰️
> A temperature sensor is needed in order to monitor the temperature on OBC Daughterboard. Last year, the OBC V1 featured an integrated temperature sensor circuit although due to time constraints, we were not able to test and iterate upon its design. The plan is to have a fully functional and tested temperature sensor which we can include in the CDR presentation (October 24th).

# Next Steps 🚶

- [ ] Check out the design for last year's temperature sensor circuit which can be found in the "OBC V1 Documentation" Word Doc.
- [ ] The components used in last year's circuit can be found in the team's 2021-2022 BOM for the OBC V1. Take a look at the datasheet for the main temperature sensor component and try to understand how this component works with the current circuit configuration.
- [ ] Research alternative configurations on the internet and determine if any changes need to be made to the current design.
- [ ] Develop a testing plan for the ciruit (LT Spice is recommended but you may also choose to build the circuit out physically and test from there).
- [ ] Complete the testing. We need proof that it works.
- [ ] Clone the latest OBC-DB KiCad files from the pcbs repository. Create the Circuit in the project's KiCad Schematic and push your changes to the pcbs repository.

# Supporting Material and Resources 📖

- [OBC V1 Documentation](https://queensuca.sharepoint.com/:w:/r/teams/GROUP-QSET/Shared%20Documents/Satellite-OBC/OBC%202021-2022/OBC%20V1%20Documentation.docx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)
- [OBC Design Document](https://queensuca.sharepoint.com/:w:/r/teams/GROUP-QSET/Shared%20Documents/Satellite-General/csdc/4000-systems-design/csdc-4500-on-board-computer-design/[csdc-4501-rpi-and-obc-db-requirements.docx](https://queensuca.sharepoint.com/:w:/r/teams/GROUP-QSET/Shared%20Documents/Satellite-General/csdc/4000-systems-design/csdc-4500-on-board-computer-design/csdc-4501-rp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)?d=w3b0bc17a7c5940788b19de2c4d372e7d&csf=1&web=1&e=qBf7Wd)
- Last year's KiCad files can be found in the pcbs repository under "STM32 Breakout"
-[STM32 Breakout](https://github.com/queens-satellite-team/pcbs/tree/master/OBC_Boards)
- [OBC Daughterboard KiCad](https://github.com/queens-satellite-team/pcbs/tree/master/OBC_Boards)

# Definition of Done 💯
> A fully tested and functional design for a temperature sensor circuit can be found in the Team's KiCad files. A description detailing your choice of components as well as circuit specifications can be found in the team's design document.

### Tags

cc: @SeanTedesco @emmapaczkowski @sirlipski @jillianmalherbe

SeanTedesco, 2023-05-23:
Temperature sensor circuit has been design and tested on the OBC-DB. Closing issue.

Closed 2023-05-23.

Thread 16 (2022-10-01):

Voltage converter circuit testing

jillianmalherbe, 2022-10-01:
# Motivation ⛰️
> We need to test last year's voltage converter circuit in LTSpice.

# Next Steps 🚶
> Provide a list of steps for someone to complete in order to finish the issue.

- [ ] Build the circuit in LTSpice using last year's components
- [ ] Test that it works in the simulation

# Supporting Material and Resources 📖

# Definition of Done 💯
> This circuit works as expected and the 5V input from EPS can be converted to 3V3. We have proof that this circuit is functional.

### Tags

cc: @SeanTedesco @emmapaczkowski @sirlipsky

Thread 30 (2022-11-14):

Daughterboard Layout

jillianmalherbe, 2022-11-14:
# Motivation ⛰️
> The layout for the OBC daughterboard needs to be completed.

# Next Steps 🚶

- [x] Refer to the high level block diagram which can be found in the OBC Design Notes when determining where to place components.
- [x] Use the correct trace width (0.5mm for 5v, 0.4mm for 3V3 and 0.2mm for data traces)
- [x] Avoid putting back traces until absolutely necessary. Try to have traces going in the same direction follow the same path.

# Supporting Material and Resources 📖

# Definition of Done 💯
> All components are placed on the board and are correctly connected using traces.

### Tags
> tag people that should know about this issue

cc: @SeanTedesco @emmapaczkowski

SeanTedesco, 2023-05-10:
OBC-DB has finished its layout, closing this issue

Closed 2023-05-10.

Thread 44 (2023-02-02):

COMM-RFB: Hardware Testing

SeanTedesco, 2023-02-02:
# Overview
The team has received the COMM-RFB (the communications board for the Selfie-Sat) and we are required to test it. This ticket is used to track the validation and improvements to the design of the COMM-RFB. Comments to this ticket are given as the board undergoes its test and improvements are identified.

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

# Supporting Document
- [COMM-RFB Requirements](https://queensuca.sharepoint.com/:w:/t/GROUP-QSET/EZjSK6CQ4oFDpKZ5OWy_wMsBu7gevlmTmQpBZuGesj0C-Q?e=rcZR5R)
- [COMM-RFB Design Document](https://queensuca.sharepoint.com/:w:/t/GROUP-QSET/EdXJe6xgnb1OosZ6rlIjX6cByBQ5YU25IqG9WcR7M_SsjA?e=bW5CMS)
- [COMM-RFB Test Plan](https://queensuca.sharepoint.com/:w:/t/GROUP-QSET/EZexL5BdUNZBvGuStJc6RWkBWZk58a7UhtpPSL9gzFSKbg?e=ZrxgEB)

SeanTedesco, 2023-02-02:
## Distance Between SMA Connectors

**Description:** The SMA connectors (J8 and J9) are located to close to one another preventing both connectors from being populated at the same time.

SeanTedesco, 2023-02-02:
## Radio Test Connector Pinout

**Description:** The radio test connector (J10) pinout does not match a direct drop-in connection to the test radio. This is desired to reduce the number of loose wires and prevent incorrect mating to the boards.

**Additional Notes:**

- _Current Radio Test Connector (J10) Pinout:_

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

- _Test Radio Pinout:_
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

**Proposed Solutions:**
1. Change KiCad schematic to reflect true RF24 test radio pinout.
2. Change KiCad PCB layout to reflect true RF24 test radio pinout.
3. Reroute connections to test radio connector (J10).

SeanTedesco, 2023-02-02:
## UART Connection

**Description:** The UART pins on the STM32 chip are not routed correctly to the PC104 bus failing to establish a connection to the OBC. On the STM32, pins PA9 and PA10 are used for UART1_Tx and UART1_Rx respectively; however, in the current schematic and layout, our routing connects COMM-TX to pin PA8 and COMM-RX to pin PA9.

**Additional Notes:**

- UART pin placement of STM32F030CCT6 chip (U1) used on the COMM-RFB

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

- Current Shematic connection of the UART pins on the COMM-RFB.
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

**Proposed Solutions:**
1. Confirm proper pins to use using STM32CubeIDE
2. Change KiCad schematic to reflect proper pins.
3. Change KiCad Layout to make use of proper pins.
4. Reroute connections from STM32 chip (U1) to PC104 connector (J1)

SeanTedesco, 2023-02-03:
## RF Front End and Guard Ring

**Description:** The RF guard ring should be made bigger to provide better EMI shielding. Additionally, the layout for the RF front end (both transmitting and receiving portions) can be optimized regarding board placement.

**Additional Notes:**
- Honestly, I think it is just not the prettiest thing to look at.
- ORCASat did a really nice job on there communications board and we could take inspiration.

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

**Proposed Solutions:**

- Use 90-degree SMA connections so cabling does not have to extend past the board edge or raise to a large height.
- Have a cutout on the PCB to allow a coax cable to be easily routed
- Increase width of RF guard ring

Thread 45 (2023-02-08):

OBC-DB: Hardware Revisions

SeanTedesco, 2023-02-08:
# Overview
The team has received the OBC-DB (a daughterboard for a Raspberry Pi to act as the on-board-computer for the Selfie-Sat) and we are required to test it. This ticket is used to track the validation and improvements to the design of the OBC-DB. Comments to this ticket are given as the board undergoes its test and improvements are identified.

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

# Supporting Documents
- [OBC-DB Requirements Document](https://queensuca.sharepoint.com/:w:/t/GROUP-QSET/EXrBCztZfHhAixneLE03Ln0B0AdDyVpprGcROt8dvMwgcA?e=CDmgXN)
- [OBc-DB Design Document](https://queensuca.sharepoint.com/:w:/t/GROUP-QSET/EUHywjQO491An0LCmfYUDX8Bj6jPBWDWJibfSH_-BiAzVA?e=hrZiR9)
- [OBC-DB Test Plan and Results](https://queensuca.sharepoint.com/:w:/t/GROUP-QSET/EVbFBM0CwGhBhxN_OX9kzYUB1b2exKB9K_VBJ6_OzT191w?e=ifoSll)

SeanTedesco, 2023-02-09:
## PCB Cut Out

**Description:** The required height of the raspberry pi away from the OBC-DB is quite large, taking up unnecessary space in the satellite and requiring a nonstandard connector to perform the dating connection.

**Additional Notes:**
No additional notes here.

**Proposed Solutions:**
Just as ORCASat has done to accommodate their SMA connector, we can create a cutout where the USB and Ethernet connectors are.

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

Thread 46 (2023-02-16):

PC/104 Breakout Board Hardware Revisions

JacobORiordanRoss, 2023-02-16:
## 🔨  A couple things that need to be fixed on the PC/104 breakout board for the Rev B:
- The pitch of the through holes for the 52-pin header is too small. The headers can be inserted but they are an interference fit which means that a quality solder joint is difficult to achieve.
- The silkscreen is flipped to where the pin numbers are upside down when the board is inserted in the board. Not a big problem but could be changed for a Rev B

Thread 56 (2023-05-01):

ADCS-CTL: Hardware Revisions

SeanTedesco, 2023-05-01:
# Overview
The team has received the ADCS-CTL (the flight controller board for the Selfie-Sat) and we are required to test it. This ticket is used to track the validation and improvements to the design of the ADCS-CTL. Comments to this ticket are given as the board undergoes its test and improvements are identified.

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

# Supporting Document
- [ADCS-CTL Requirements](https://queensuca.sharepoint.com/:w:/t/GROUP-QSET/EcNbziCC9QVGmPCA9BvpPYwBgKOJUJ3NwYG8GcVttTkj3Q?e=GmZuC9)
- [ADCS-CTL Design](https://queensuca.sharepoint.com/:w:/t/GROUP-QSET/ETTnWEADMsFBrCl-_SiXy10B0_uddFnf6f9SpKADB_iiCA?e=dLy06Z)
- [ADCS-CTL Test Plan](https://queensuca.sharepoint.com/:w:/t/GROUP-QSET/EXfhTwfIQh5GqMT7il1ZJkQBfekypSBG5K0AnU5QByKRZw?e=pAc22G)

SeanTedesco, 2023-05-02:
# Rerouting for PWM signals

**Description**: Device U1 (STM32F103RET6) needs to provide PWM signals for the _RAMP_CTL_ and the _PWM_SET_ pins going to the motor controllers for the reaction wheels. As found by @Aidan-Sheedy, some of the output signals from the STM32 are not PWM compatible but go to the motor controller anyway.

**Additional Notes**: As seen below, _ADCS_GPIO_RW4_PWM_SET_ is not a GPIO but requires a channel of a timer. And all 4x of the ADCS_GPIO_RWx_RAMP signals are also not GPIOs but require connection to the channels of a timer.

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

**Proposed Solutions**:
- swap signal _ADCS_GPIO_RW4_DIR_ on the STM32's TIM1_CH1 pin with the current _ADCS_GPIO_RW4_PWM_SET_ signal.
- swap signal _ADCS_GPIO_3V3_SYS1 on the STM32's TIM8_CH2 pin with the current _ADCS_GPIO_RW1_RAMP_ signal.
- swap signal _ADCS_GPIO_3V3_SYS2 on the STM32's TIM8_CH3 pin with the current _ADCS_GPIO_RW2_RAMP_ signal.
- leave _ADCS_GPIO_RW3_RAMP_ and _ADCS_GPIO_RW4_RAMP_ as is, and have no ramp control on these motor controllers.

SeanTedesco, 2023-05-03:
Regarding **Issue 1: Rerouting for PWM signals**, a jumper wire was installed connecting the physical Pin 45 to the pad of Pin 41 (routed to _ADCS_GPIO_RW4_DIR_) of U1 (STM32) as seen below.

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

The next step is to install another jumper wire connecting Pin 41 on U1 (STM32) to the pad of Pin 45 (routed to _ADCS_GPIO_RW4_PWM_SET_)

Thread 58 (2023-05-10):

RWL-DB Hardware Revisions

SeanTedesco, 2023-05-10:
# Overview
The team has received the RWL-DB (a daughterboard for the ADCS-CTL to interface with the maxon reaction wheels) and we are required to test it. This ticket is used to track the validation and improvements to the design of the RWL-DB. Comments to this ticket are given as the board undergoes its test and improvements are identified.

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

# Supporting Documents
- [RWL-DB Requirements](https://queensuca.sharepoint.com/:w:/t/GROUP-QSET/EUsCxLiAdTdJqYZeZz5m_94BhnJ1BmrDscmn9r9qEvCqbA?e=qkSz2D)
- [RWL-DB Design](https://queensuca.sharepoint.com/:w:/t/GROUP-QSET/EdL7FDZ2STpIskX9oXvkuAwBZT0fBcegMcX3pFZHU9nleA?e=v5UyGV)
- [RWL-DB Test Plan](https://queensuca.sharepoint.com/:w:/t/GROUP-QSET/EaKqyzXfdsVFo9oBMZ5b2y8BnRyXFQTClveMdgEjEaSYJA?e=j0zQNq)

SeanTedesco, 2023-05-10:
# Incorrect Connections to ESCON Motor Controllers

**Problem**
The motor control signals from J1 (main PC104 connector) do not map to the correct pins the the individual motor controllers in order for nominal operation.

**Additional Information**
As seen below, using ESCON Studio to set the firmware of the motor controllers, the expected inputs to the motor controller are:
- Digital Input 2: Direction
- Digital Input 4: Enable
- Analog Input 1: RPM Set Value (PWM)
- Analog Input 2: Ramp Control (PWM)

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

These digital and analog inputs map to the motor controller pins:
- Pin 14: Digital Input 4: Enable
- Pin 16: Digital Input 2: Direction
- Pin 22: Analog Input 2: Ramp Control (PWM)
- Pin 24: Analog Input 1: RPM Set Value (PWM)

However, looking at the current schematic below, we see that the Enable and Direction signals are correctly routed to Pin 14 and Pin 16; however, the Ramp Control signal is routed to Pin 24 instead of Pin 22, and the RPM Set Value is routed to pin 17 instead of Pin 24

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

Regarding Issue #56, we already don't have ramp control, so the incorrect routing for this can be ignored for now. Thus, we can solder a jumper connecting Pin 22 and Pin 24 together and disable the ramp control circuitry by desoldering the series components going to the motor controller.

**Proposed Solution**
For next iteration:
1. Reroute signals to proper pins on motor controller

For this iteration:
1. Desolder all motor controllers from RWL-DB
3. Write down desired firmware settings in Test Plan
4. Use ESCON studio to upload correct firmware settings to each motor controller
5. Use Arduino and single reaction wheel to validate motor controller firmware settings (it turns on, can be enabled/disabled, etc)
6. Solder jumper connecting
7. Solder all motor controllers back onto RWL-DB
8. Connect all motors and test all 4 motor controllers

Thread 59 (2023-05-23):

ALL: System on Module Implementation

SeanTedesco, 2023-05-23:
# Overview
This ticket is used to track the discussion on moving towards a System on Module (SoM) implementation for QSET's hardware. An SoM provides the core components of an embedded processing system, including the processor, decoupling capacitors, crystals, external memory on a single small board which then can be mated to a motherboard providing the required sub-system specific features. An example of a SoM and a mother board is given below:

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

### Pros:
- Hardware development may be cheaper as hardware revisions no longer need to repurchase these core components.
- Hardware development is further standardized across all sub-systems.
- Firmware development is made more consistent as the same microcontroller can be used across many sub-systems.

### Cons:
- Most sub-systems require drastically different microcontroller specifications (timer channels, serial communication, analog input and output, etc.)

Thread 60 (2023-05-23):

ALL: Incorrect Pinout For All PC104 Headers

SeanTedesco, 2023-05-23:
# Overview
All QSET-developed boards are incompatible with the Clyde Space EPS module. The team is currently using a PC104 header to connect all electronics on the satellite. Each one of the boards developed by QSET was intended to work with the off-the-shelf EPS module provided by Clyde Space through the PC104 header; however, the QSET boards were designed with the PC104 header rotated 180 degrees.

As seen in the images below, Pin 1 on the Clyde Space board is located on the left hand side of the PCB, while Pin 1 on all QSET boards are located on the right hand side.

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

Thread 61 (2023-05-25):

BAT-DB: Hardware Revisions

SeanTedesco, 2023-05-25:
# Overview
The team has received the BAT-DB (battery board used with the EPS system to provide power storage for the satellite) and we are required to test it. This ticket is used to track the validation, issues, and improvements to the design of the BAT-DB. Comments to this ticket are given as the board undergoes its test and improvements are identified.

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

# Supporting Documents
- [Battery Board Requirements](https://queensuca.sharepoint.com/:w:/t/GROUP-QSET/EQtAdzk_EARIrMd4tkivvn8BwNerQp--YzVH_r26aHvoOQ?e=Hxiomy)
- [Battery Board Design](https://queensuca.sharepoint.com/:w:/t/GROUP-QSET/EWqJf31M83NMuHhEOlDTnKcBC-Sz5hyvzvNoyW-eYluKog?e=LJZ6em)
- [Battery Board Test Plan](https://queensuca.sharepoint.com/:w:/t/GROUP-QSET/EWVV9Ow1So5EnTouTD9SN1QBBHr0qF3FQgiTU-P9vqx81w?e=55cOZF)

griffinjones1, 2023-05-25:
c10 (0204 size) was lost in trying to repair a reflow error. decoupling capacitor for timer LTC6995 (U4). will function fine without but add back in future iterations.

griffinjones1, 2023-05-28:
power control schematic - change flight model and eng model jumper design to be the same for J7 and J9 in order to reduce confusion. Currently one is in parallel and the other is in series.

griffinjones1, 2023-05-28:
Many more test points needed - live list:
- BCR_OUT
- 5V CHG input
- PCM_IN
- GND

a clean list of TPs on the front page of schematic will be good for easy reference

griffinjones1, 2023-05-29:
watchdog and deployment timer pins are messed up and shorted to ground. fix these pins for next iteration

griffinjones1, 2023-05-29:
battery clips are too close together - clips contact each other and short batteries when installed.
also test connector pcb cannot fit in J3 when a battery is installed.

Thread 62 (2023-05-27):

UMB-DB: Hardware Revisions

SeanTedesco, 2023-05-27:
The team has received the UMB-DB (a debugging toll for QSET hardware) and we are required to test it. This ticket is used to track the validation and improvements to the design of the UMB-DB. Comments to this ticket are given as the board undergoes its test and improvements are identified.

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

SeanTedesco, 2023-05-27:
During the sprint for competition the ADCS-CTO board was being codded using the UMB-DB and when set up later after bein taken apart it bricked. It was determined that the 3.3V had shorted. After discussion and review it was determined that the short was due to the UMB-DB was powered and was briefly connected wrong due the pins being finicky to connect and could slip into the wrong slots. The redesign should make the pins unable to be connected unless they are correctly positioned.

jillianmalherbe, 2023-05-30:
Next iteration of the debug board should feature an LED that shows when the board is receiving power.

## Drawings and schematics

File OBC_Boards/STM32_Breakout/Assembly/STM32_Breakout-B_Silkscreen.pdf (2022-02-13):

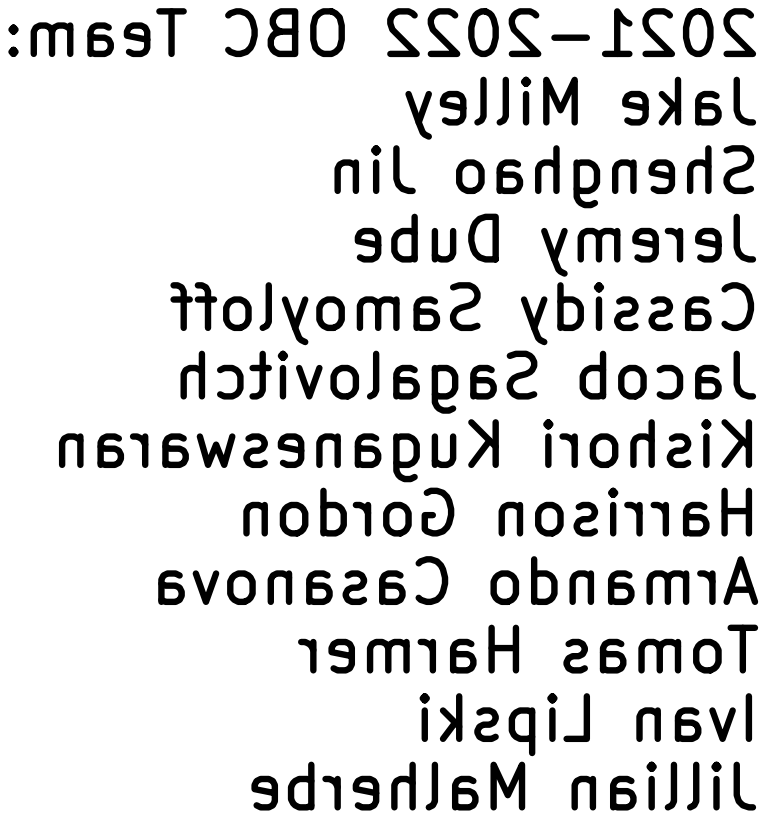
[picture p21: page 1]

2021-2022 OBC Team: Jake Milley Shenghao Jin

Jeremy Dube Cassidy Samoyloff Jacob Sagalovitch Kishori Kuganeswaran Harrison Gordon Armando Casanova Tomas Harmer

Ivan Lipski Jillian Malherbe

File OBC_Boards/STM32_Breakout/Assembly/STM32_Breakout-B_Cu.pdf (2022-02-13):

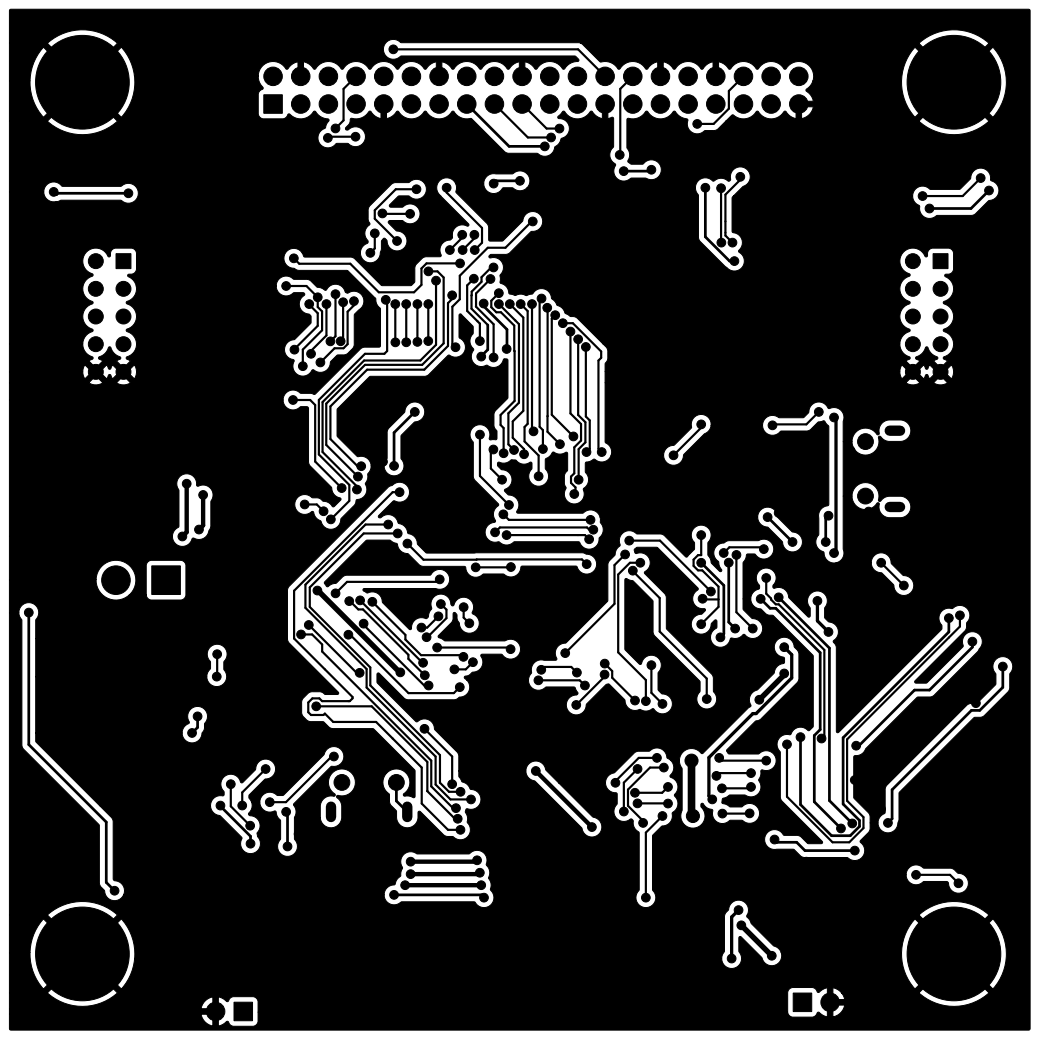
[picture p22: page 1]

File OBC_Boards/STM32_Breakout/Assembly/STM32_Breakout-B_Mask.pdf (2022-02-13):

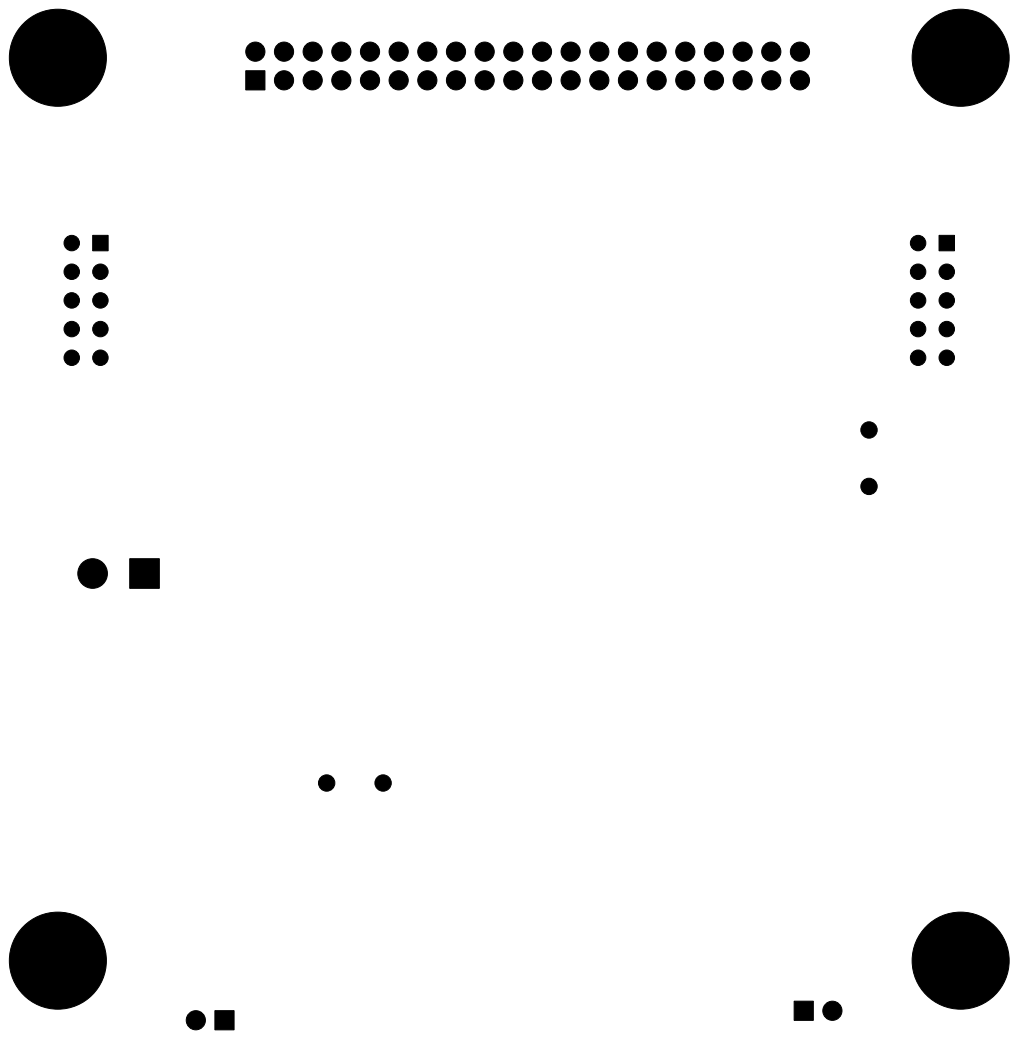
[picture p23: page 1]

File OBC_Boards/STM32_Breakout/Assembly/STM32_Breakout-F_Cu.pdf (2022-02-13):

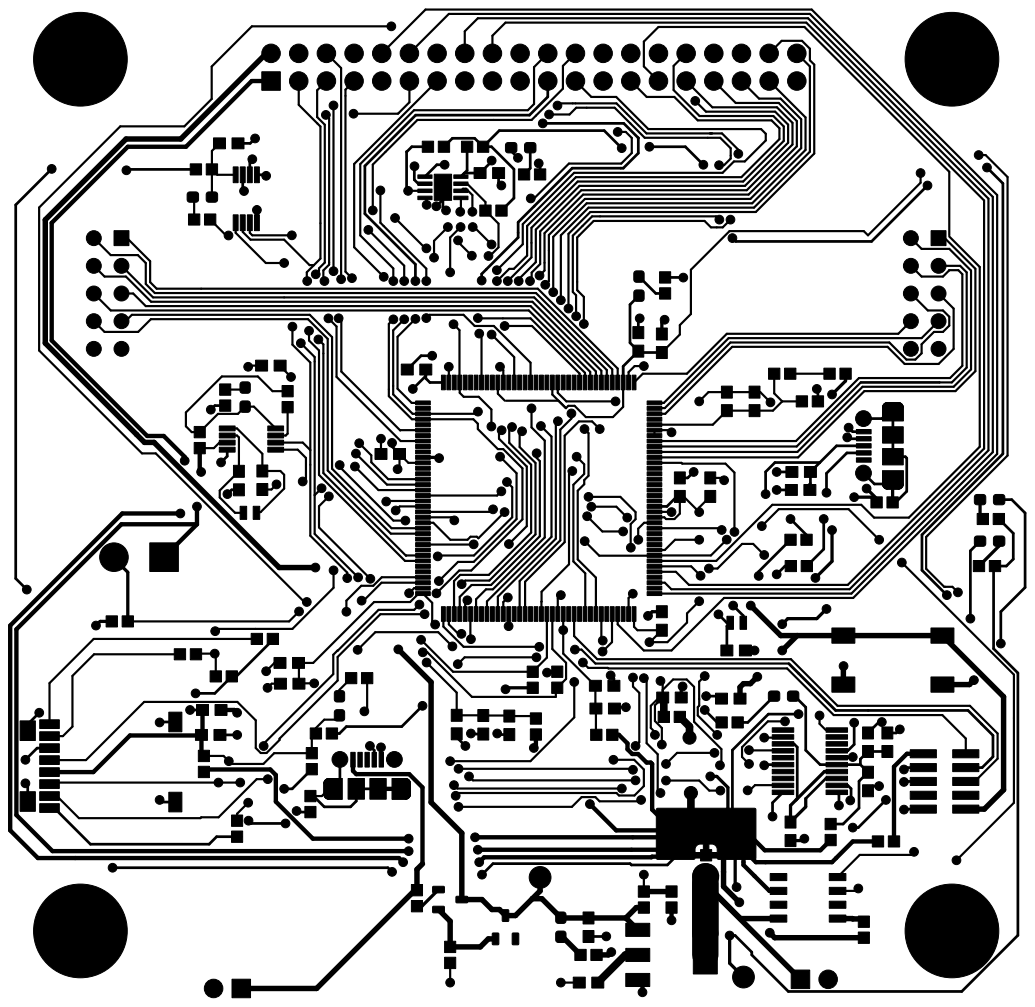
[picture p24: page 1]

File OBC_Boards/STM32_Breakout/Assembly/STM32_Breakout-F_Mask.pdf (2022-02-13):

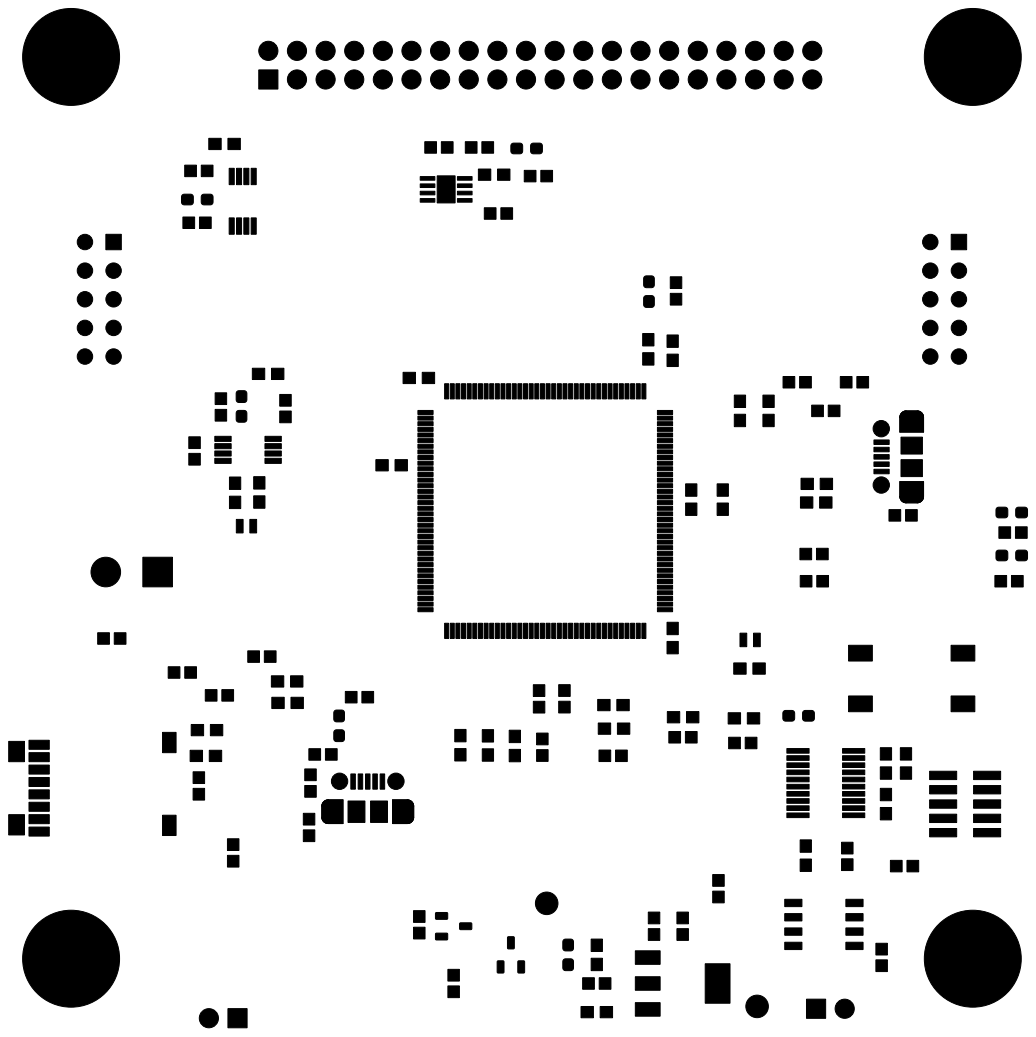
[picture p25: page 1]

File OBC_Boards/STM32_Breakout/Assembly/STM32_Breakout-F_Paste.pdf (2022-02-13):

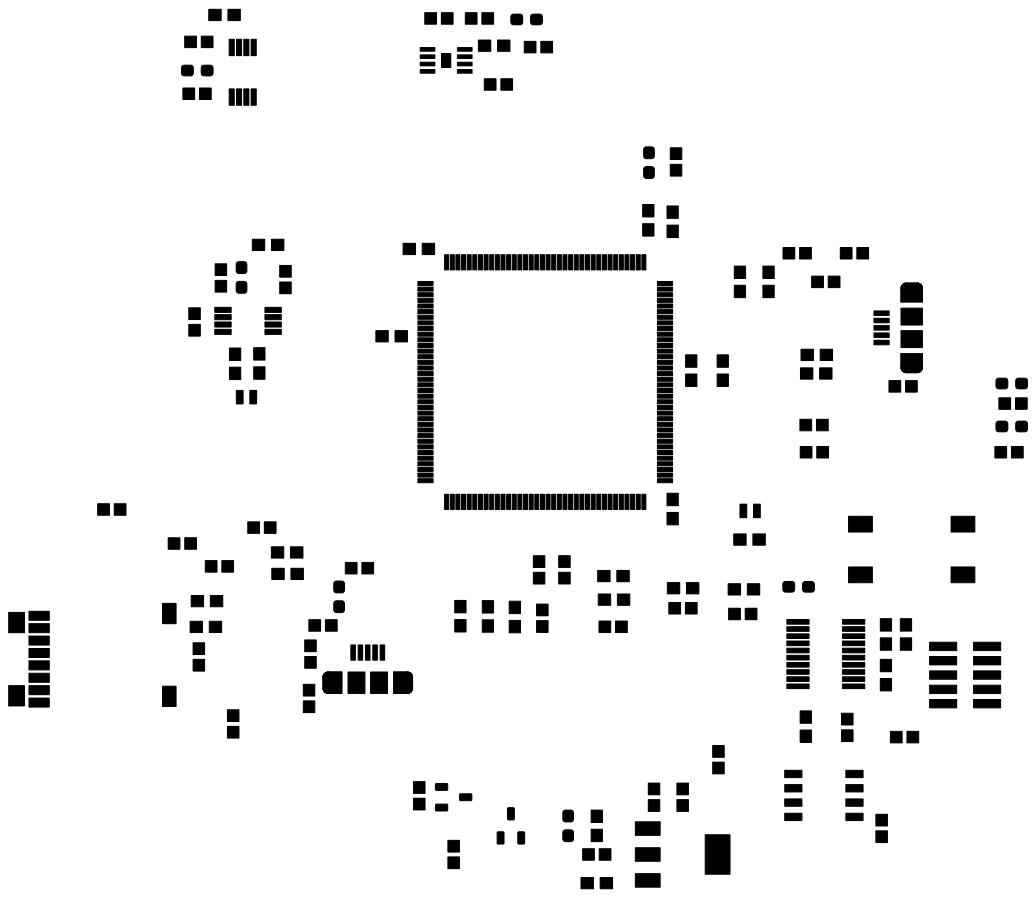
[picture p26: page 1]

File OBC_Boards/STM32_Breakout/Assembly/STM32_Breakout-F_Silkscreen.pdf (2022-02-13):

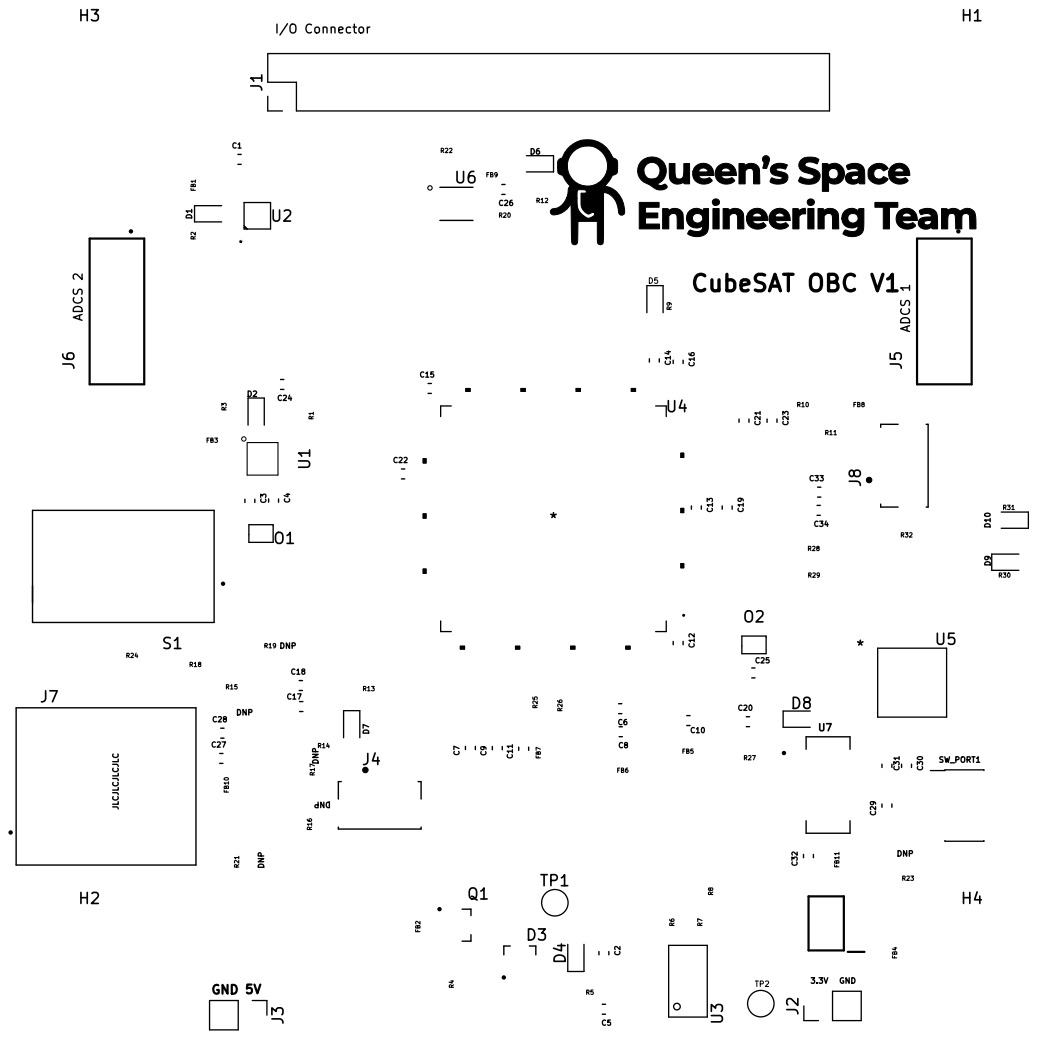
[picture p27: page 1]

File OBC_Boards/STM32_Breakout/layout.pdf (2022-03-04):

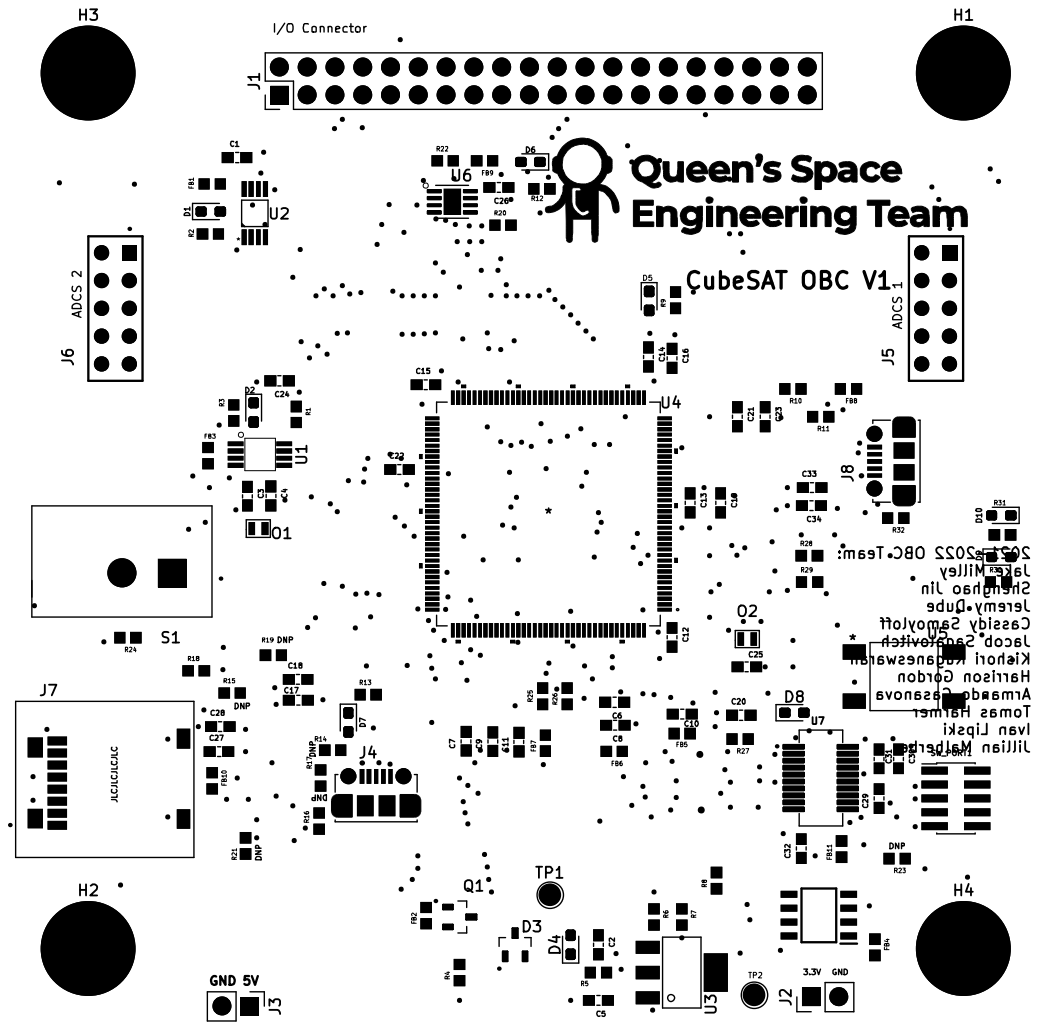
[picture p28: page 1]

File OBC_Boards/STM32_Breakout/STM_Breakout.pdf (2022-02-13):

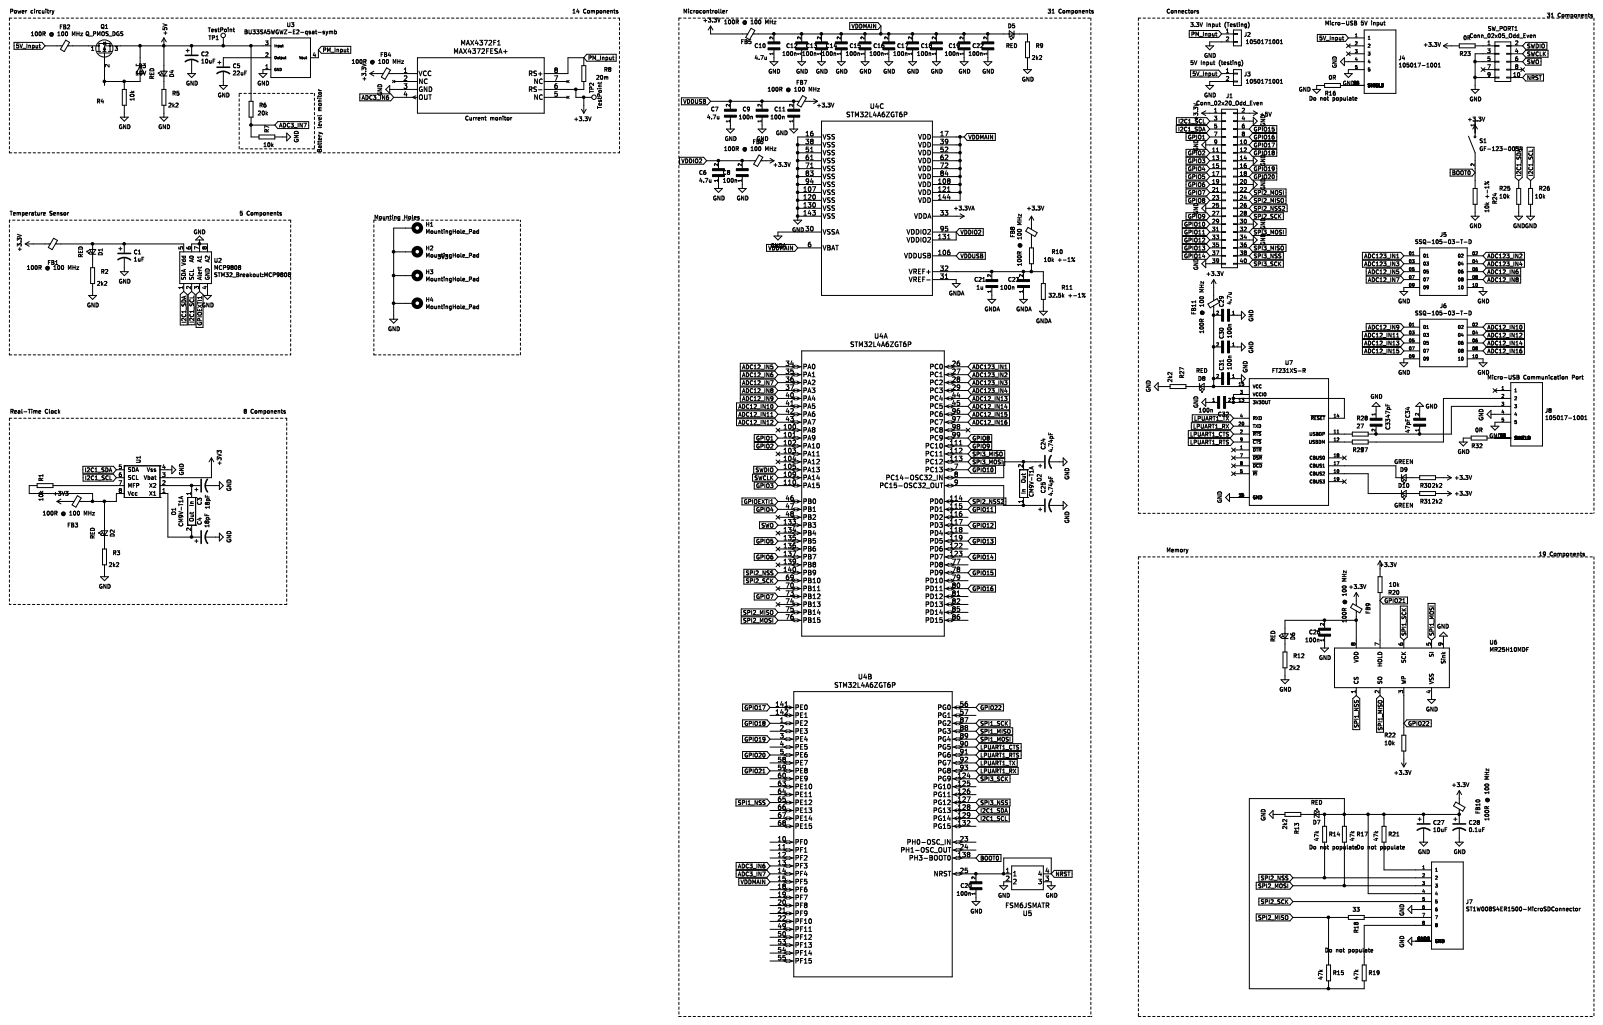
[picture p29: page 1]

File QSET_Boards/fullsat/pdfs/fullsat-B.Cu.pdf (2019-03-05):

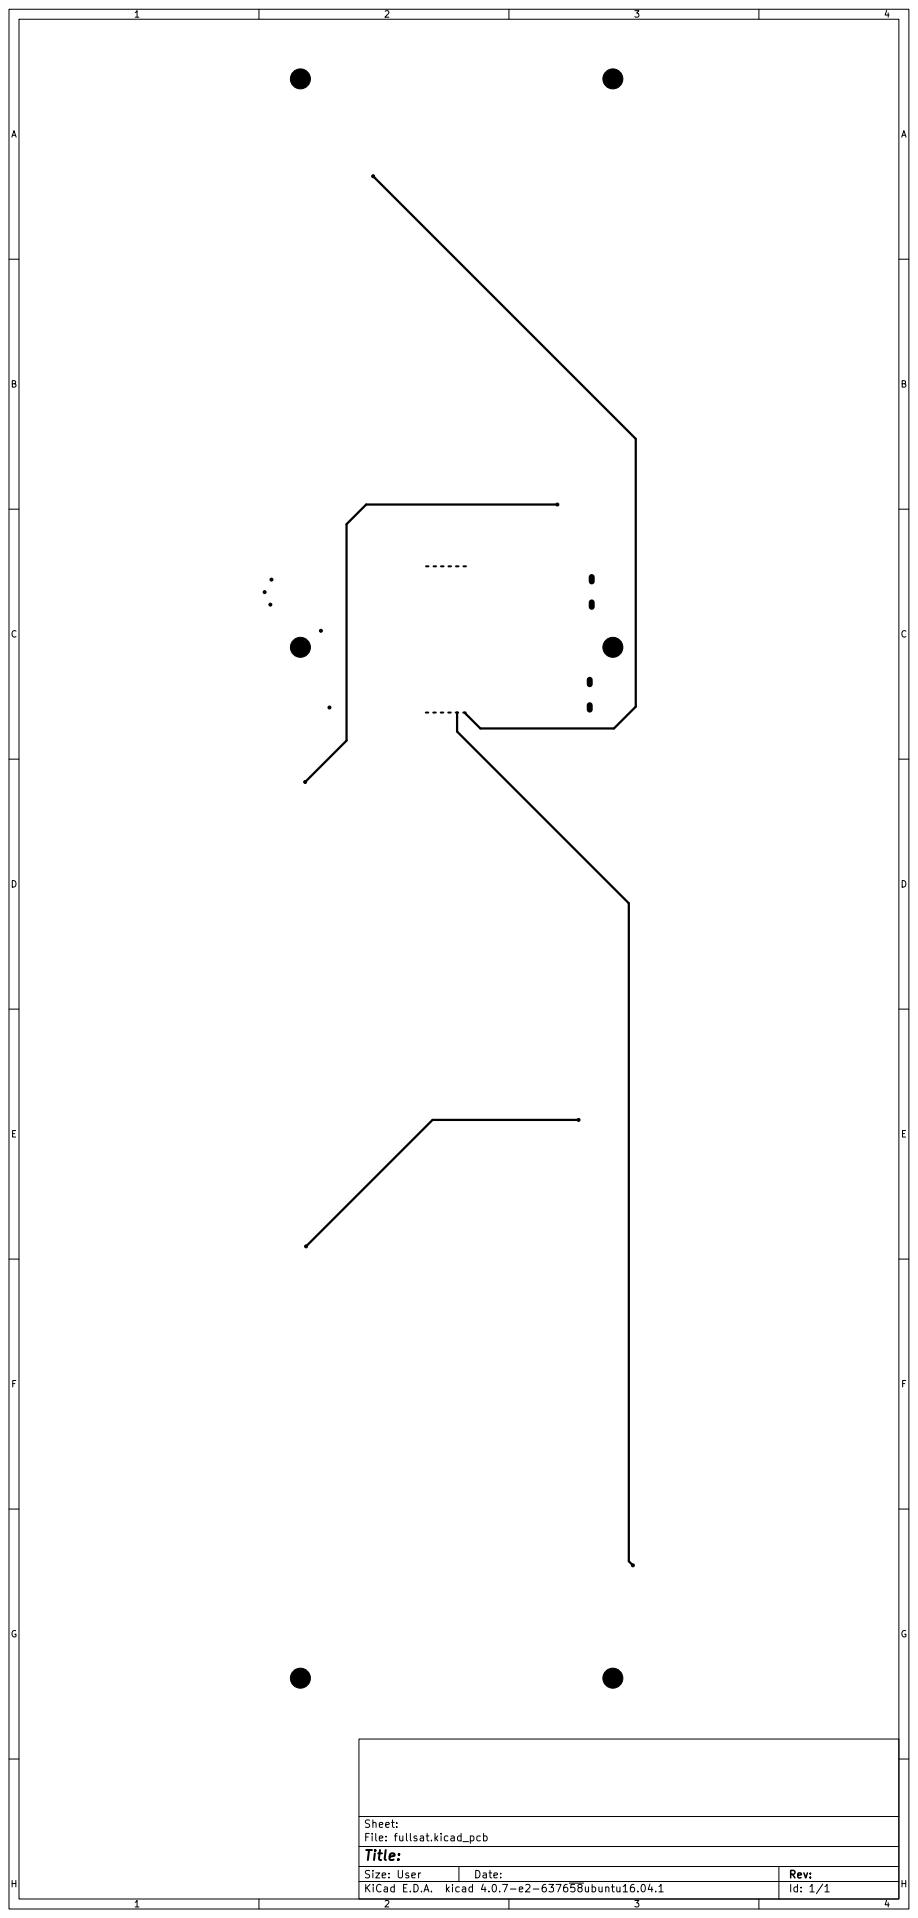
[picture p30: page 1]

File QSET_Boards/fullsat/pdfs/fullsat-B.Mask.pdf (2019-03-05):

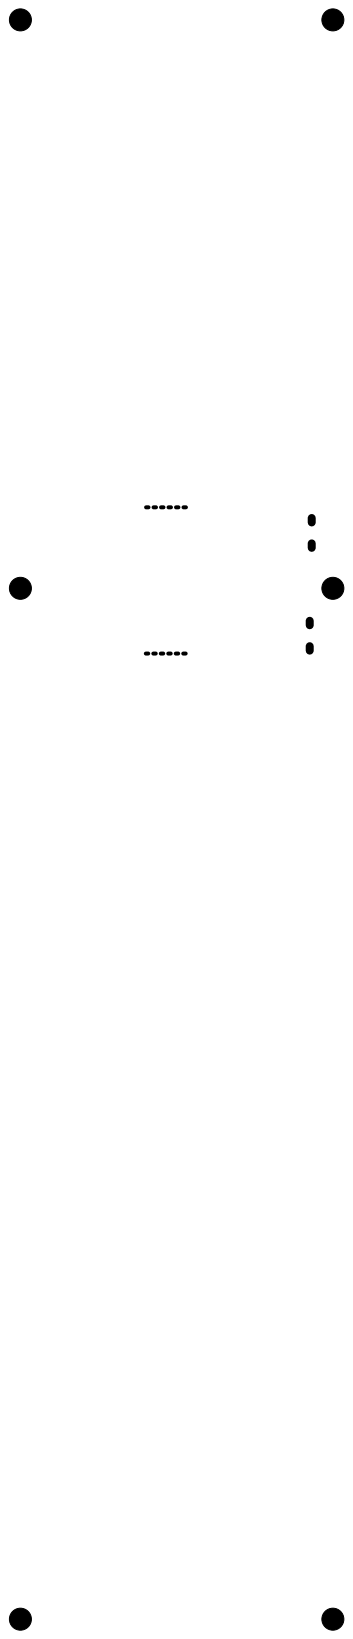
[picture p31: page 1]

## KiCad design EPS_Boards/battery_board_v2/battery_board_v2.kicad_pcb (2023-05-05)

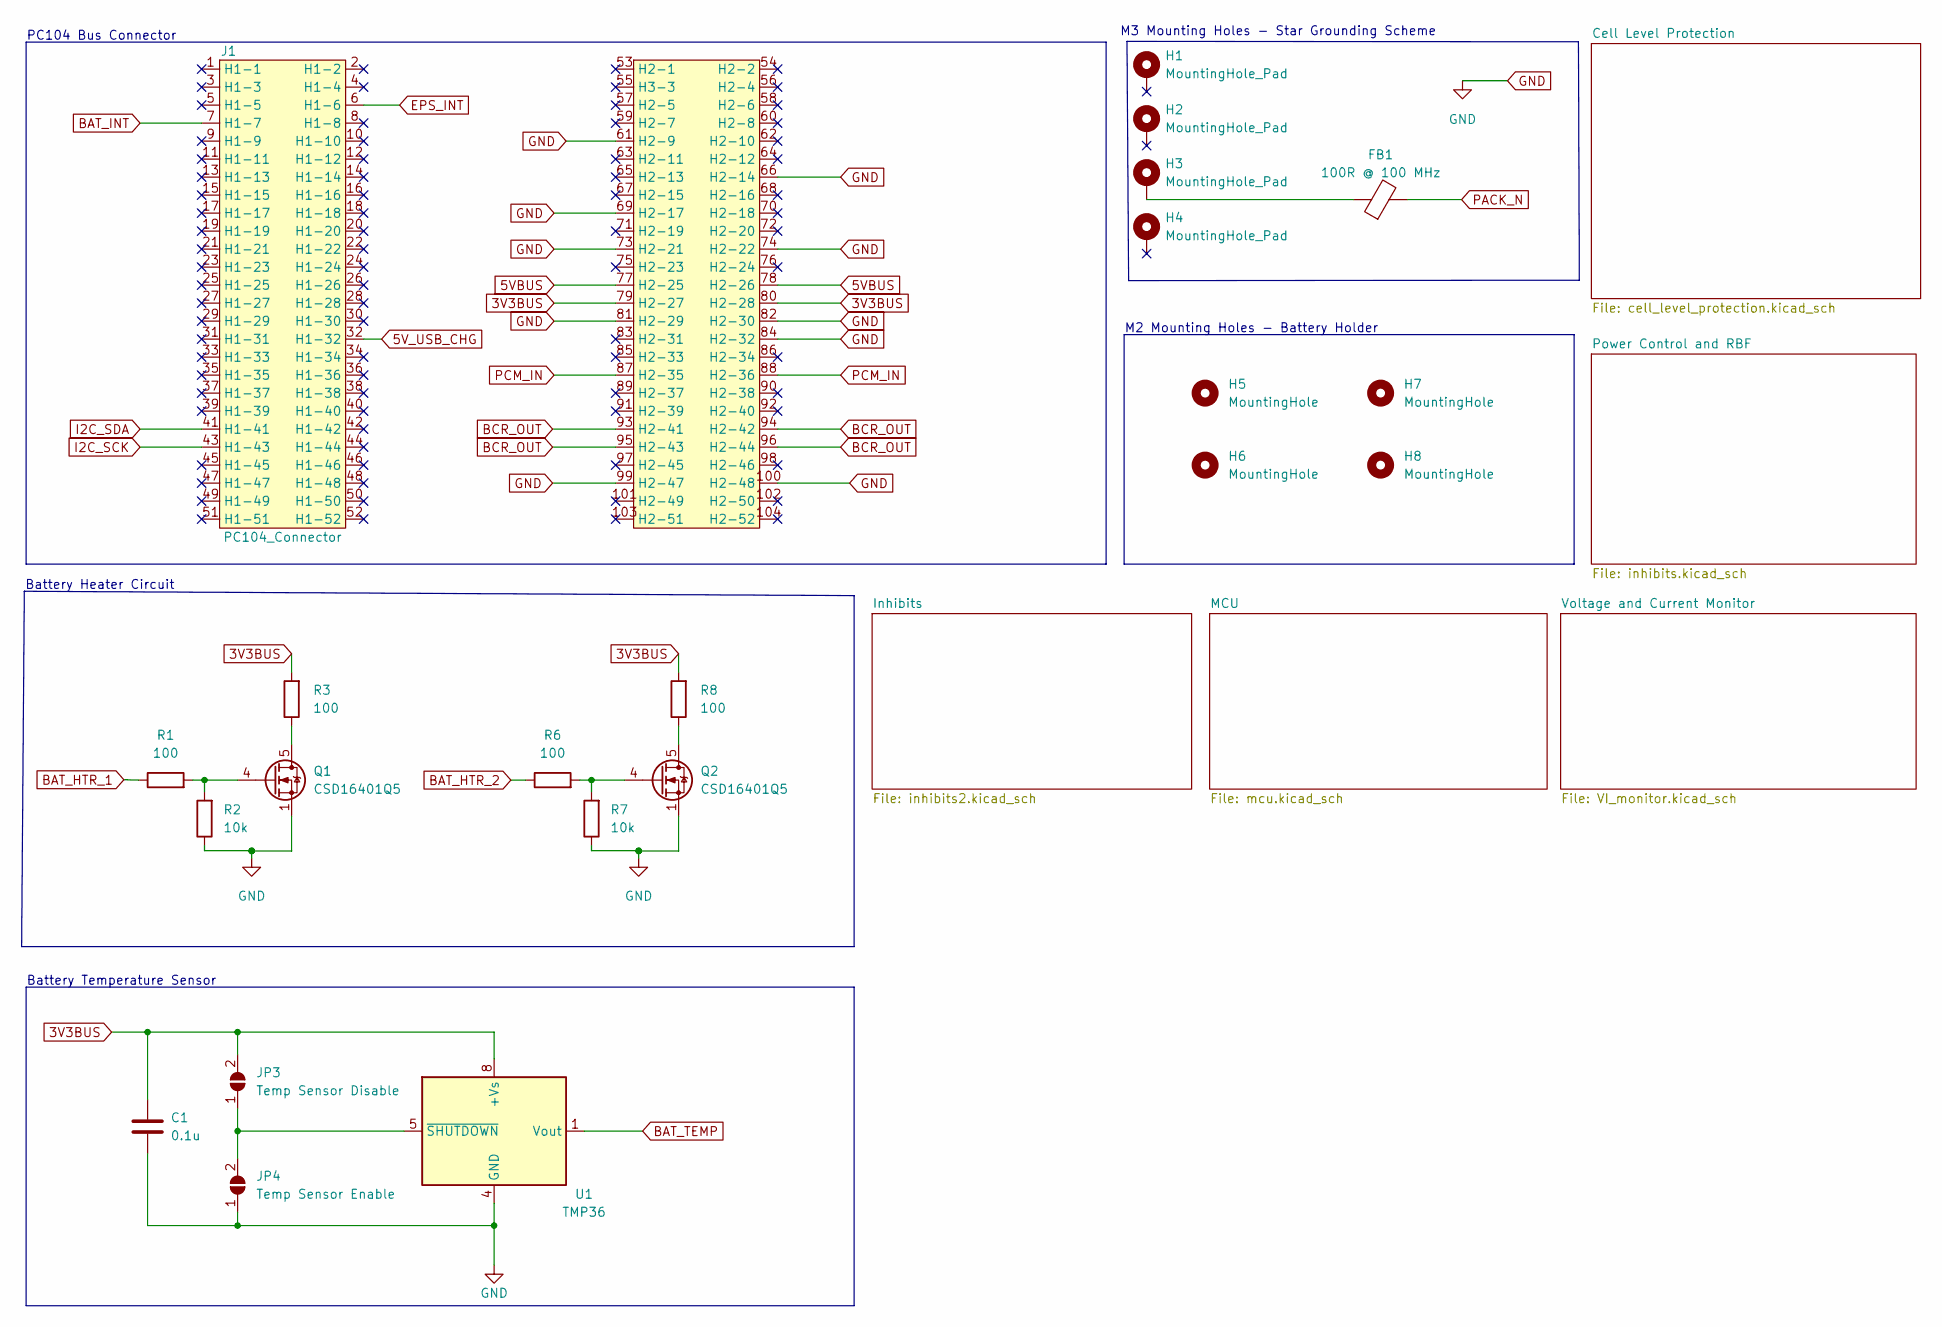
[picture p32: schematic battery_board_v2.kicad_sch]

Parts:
C1: 0.1u; C_0402_1005Metric
FB1: 100R @ 100 MHz; L_0603_1608Metric
H1, H2, H3, H4: MountingHole_Pad; MountingHole_3.2mm_M3_Pad_TopBottom
H5, H6, H7, H8: MountingHole; MountingHole_2.2mm_M2_DIN965_Pad
J1: PC104_Connector; pc104-connector
JP3: Temp Sensor Disable; SolderJumper-2_P1.3mm_Open_Pad1.0x1.5mm
JP4: Temp Sensor Enable; SolderJumper-2_P1.3mm_Open_Pad1.0x1.5mm
Q1, Q2: CSD16401Q5; TDSON-8-1
R1, R6: 100; R_0402_1005Metric
R2, R7: 10k; R_0402_1005Metric
R3, R8: 100; R_Axial_DIN0207_L6.3mm_D2.5mm_P7.62mm_Horizontal
U1: TMP36; SOIC-8_3.9x4.9mm_P1.27mm

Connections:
3V3BUS: C1.1, J1.79 (H2-27), J1.80 (H2-28), JP3.2 (B), R3.2, R8.2, U1.8 (+Vs); also elsewhere on the board
5VBUS: J1.77 (H2-25), J1.78 (H2-26)
5V_USB_CHG: J1.32 (H1-32)
BAT_HTR_1: R1.1; also elsewhere on the board
BAT_HTR_2: R6.1; also elsewhere on the board
BAT_INT: J1.7 (H1-7); also elsewhere on the board
BAT_TEMP: U1.1 (Vout); also elsewhere on the board
BCR_OUT: J1.93 (H2-41), J1.94 (H2-42), J1.95 (H2-43), J1.96 (H2-44); also elsewhere on the board
EPS_INT: J1.6 (H1-6); also elsewhere on the board
GND: C1.2, J1.61 (H2-9), J1.66 (H2-14), J1.69 (H2-17), J1.73 (H2-21), J1.74 (H2-22), J1.81 (H2-29), J1.82 (H2-30), J1.84 (H2-32), J1.99 (H2-47), J1.100 (H2-48), JP4.1 (A), Q1.1 (S), Q1.2 (S), Q1.3 (S), Q2.1 (S), Q2.2 (S), Q2.3 (S), R2.1, R7.1, U1.4 (GND); also elsewhere on the board
I2C_SCK: J1.43 (H1-43); also elsewhere on the board
I2C_SDA: J1.41 (H1-41); also elsewhere on the board
unnamed: FB1.1, H3.1
unnamed: JP3.1 (A), JP4.2 (B), U1.5 (~SHUTDOWN)
unnamed: Q1.4 (G), R1.2, R2.2
unnamed: Q1.5 (D), R3.1
unnamed: Q2.4 (G), R6.2, R7.2
unnamed: Q2.5 (D), R8.1
PACK_N: FB1.2; also elsewhere on the board
PCM_IN: J1.87 (H2-35), J1.88 (H2-36); also elsewhere on the board

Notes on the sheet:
M2 Mounting Holes - Battery Holder
Battery Temperature Sensor
Battery Heater Circuit
PC104 Bus Connector
M3 Mounting Holes - Star Grounding Scheme

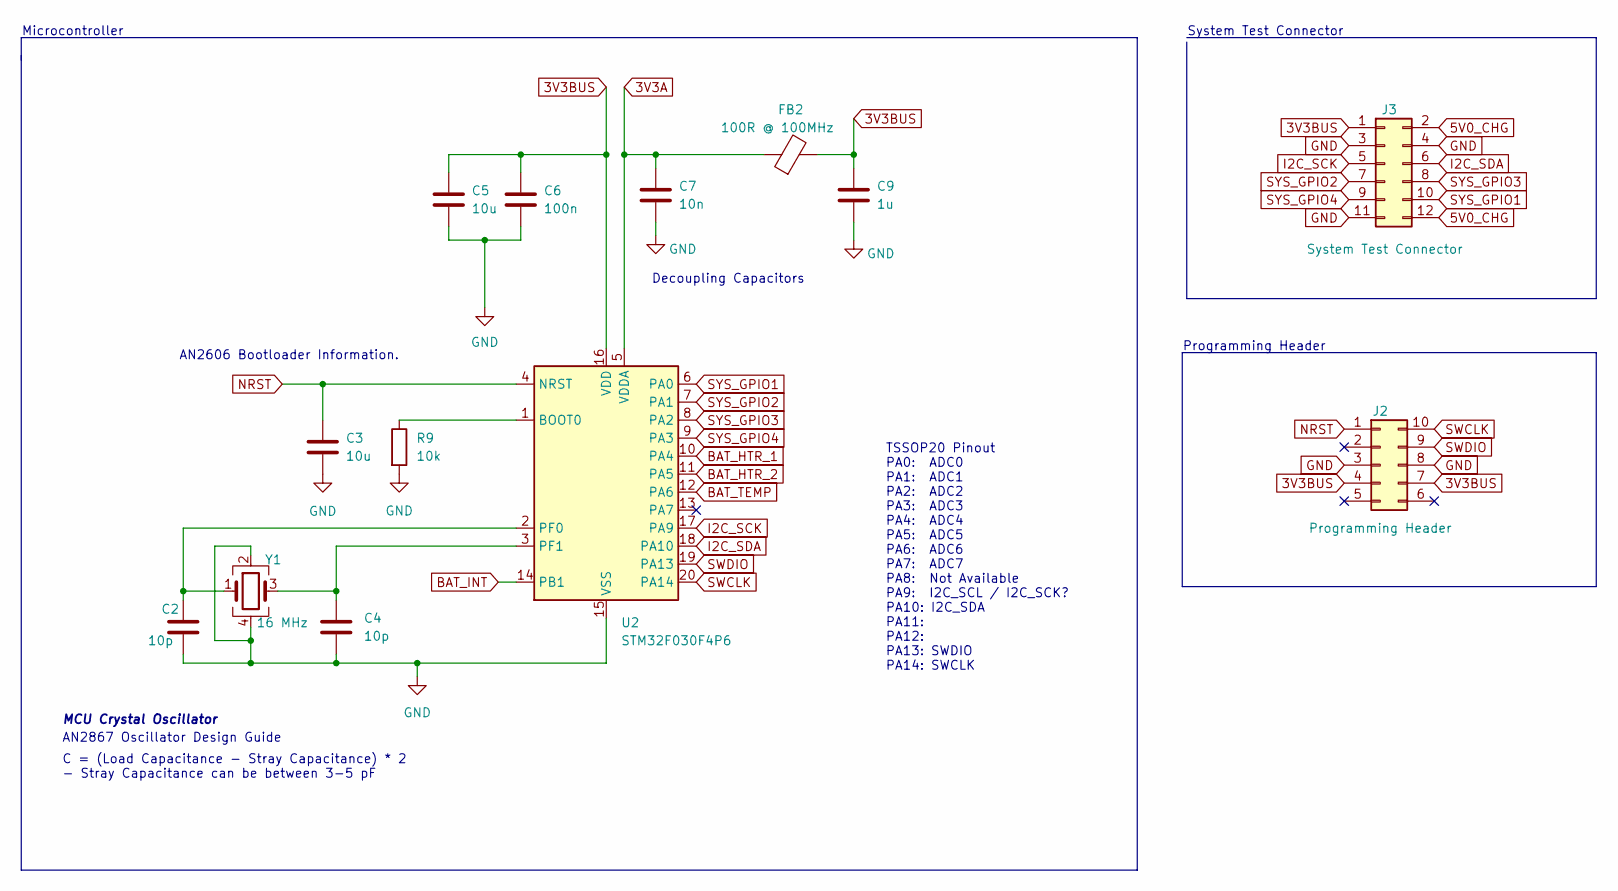
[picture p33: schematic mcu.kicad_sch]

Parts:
C2, C4: 10p; C_0402_1005Metric
C3, C5: 10u; C_0402_1005Metric
C6: 100n; C_0402_1005Metric
C7: 10n; C_0402_1005Metric
C9: 1u; C_0402_1005Metric
FB2: 100R @ 100MHz; L_0402_1005Metric
J2: Programming Header; PinSocket_2x05_P2.54mm_Vertical
J3: System Test Connector; PinSocket_2x06_P2.54mm_Vertical
R9: 10k; R_0402_1005Metric
U2: STM32F030F4P6; TSSOP-20_4.4x6.5mm_P0.65mm
Y1: 16 MHz; Crystal_SMD_3225-4Pin_3.2x2.5mm

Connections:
3V3A: C7.1, FB2.1, U2.5 (VDDA)
3V3BUS: C5.1, C6.1, C9.1, FB2.2, J2.4, J2.7, J3.1, U2.16 (VDD); also elsewhere on the board
5V0_CHG: J3.2, J3.12; also elsewhere on the board
BAT_HTR_1: U2.10 (PA4); also elsewhere on the board
BAT_HTR_2: U2.11 (PA5); also elsewhere on the board
BAT_INT: U2.14 (PB1); also elsewhere on the board
BAT_TEMP: U2.12 (PA6); also elsewhere on the board
GND: C2.2, C3.2, C4.2, C5.2, C6.2, C7.2, C9.2, J2.3, J2.8, J3.3, J3.4, J3.11, R9.2, U2.15 (VSS), Y1.2, Y1.4; also elsewhere on the board
I2C_SCK: J3.5, U2.17 (PA9); also elsewhere on the board
I2C_SDA: J3.6, U2.18 (PA10); also elsewhere on the board
NRST: C3.1, J2.1, U2.4 (NRST)
unnamed: C2.1, U2.2 (PF0), Y1.1
unnamed: C4.1, U2.3 (PF1), Y1.3
unnamed: R9.1, U2.1 (BOOT0)
SWCLK: J2.10, U2.20 (PA14)
SWDIO: J2.9, U2.19 (PA13)
SYS_GPIO1: J3.10, U2.6 (PA0)
SYS_GPIO2: J3.7, U2.7 (PA1)
SYS_GPIO3: J3.8, U2.8 (PA2)
SYS_GPIO4: J3.9, U2.9 (PA3)

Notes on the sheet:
System Test Connector
AN2867 Oscillator Design Guide
C = (Load Capacitance - Stray Capacitance) * 2 - Stray Capacitance can be between 3-5 pF
Programming Header
Decoupling Capacitors
TSSOP20 Pinout PA0: ADC0 PA1: ADC1 PA2: ADC2 PA3: ADC3 PA4: ADC4 PA5: ADC5 PA6: ADC6 PA7: ADC7 PA8: Not Available PA9: I2C_SCL / I2C_SCK? PA10: I2C_SDA PA11: PA12: PA13: SWDIO PA14: SWCLK
MCU Crystal Oscillator
Microcontroller
AN2606 Bootloader Information.

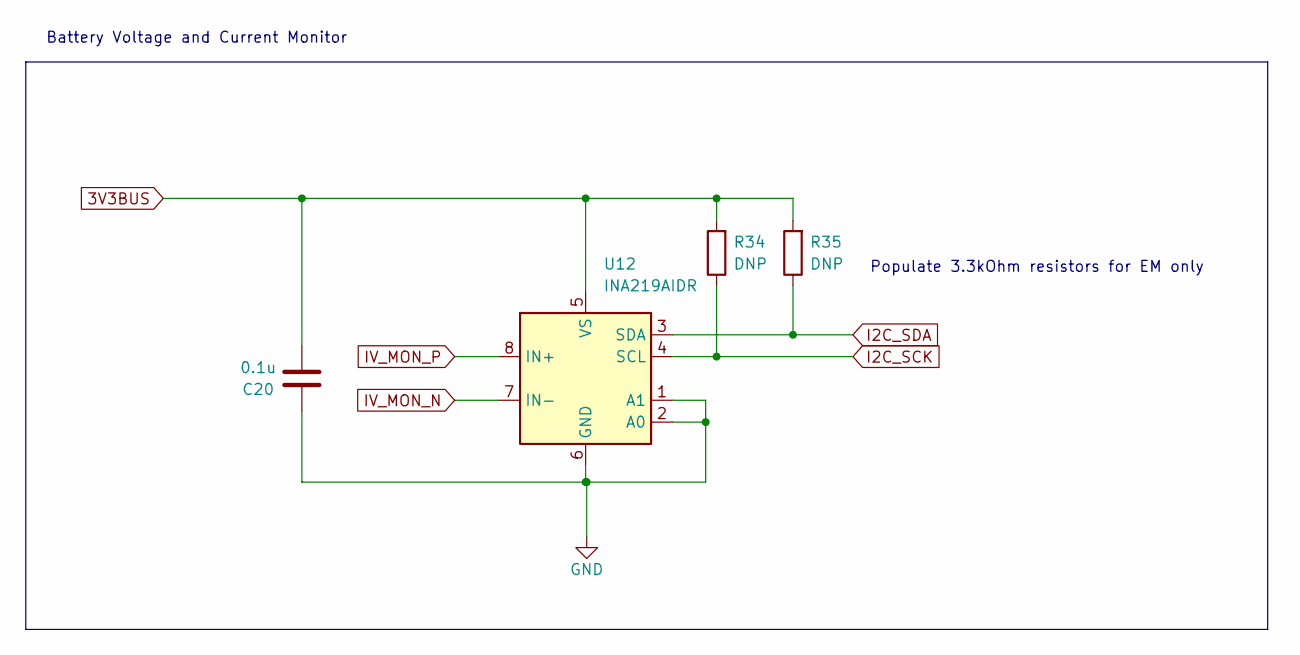
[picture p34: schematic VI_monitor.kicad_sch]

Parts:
C20: 0.1u; C_0402_1005Metric
R34, R35: DNP; R_0603_1608Metric
U12: INA219AIDR; SOIC-8_3.9x4.9mm_P1.27mm

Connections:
3V3BUS: C20.2, R34.2, R35.2, U12.5 (VS); also elsewhere on the board
BCR_OUT: U12.8 (IN+); also elsewhere on the board
GND: C20.1, U12.1 (A1), U12.2 (A0), U12.6 (GND); also elsewhere on the board
I2C_SCK: R34.1, U12.4 (SCL); also elsewhere on the board
I2C_SDA: R35.1, U12.3 (SDA); also elsewhere on the board
IV_MON_N: U12.7 (IN-); also elsewhere on the board

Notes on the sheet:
Battery Voltage and Current Monitor
Populate 3.3kOhm resistors for EM only

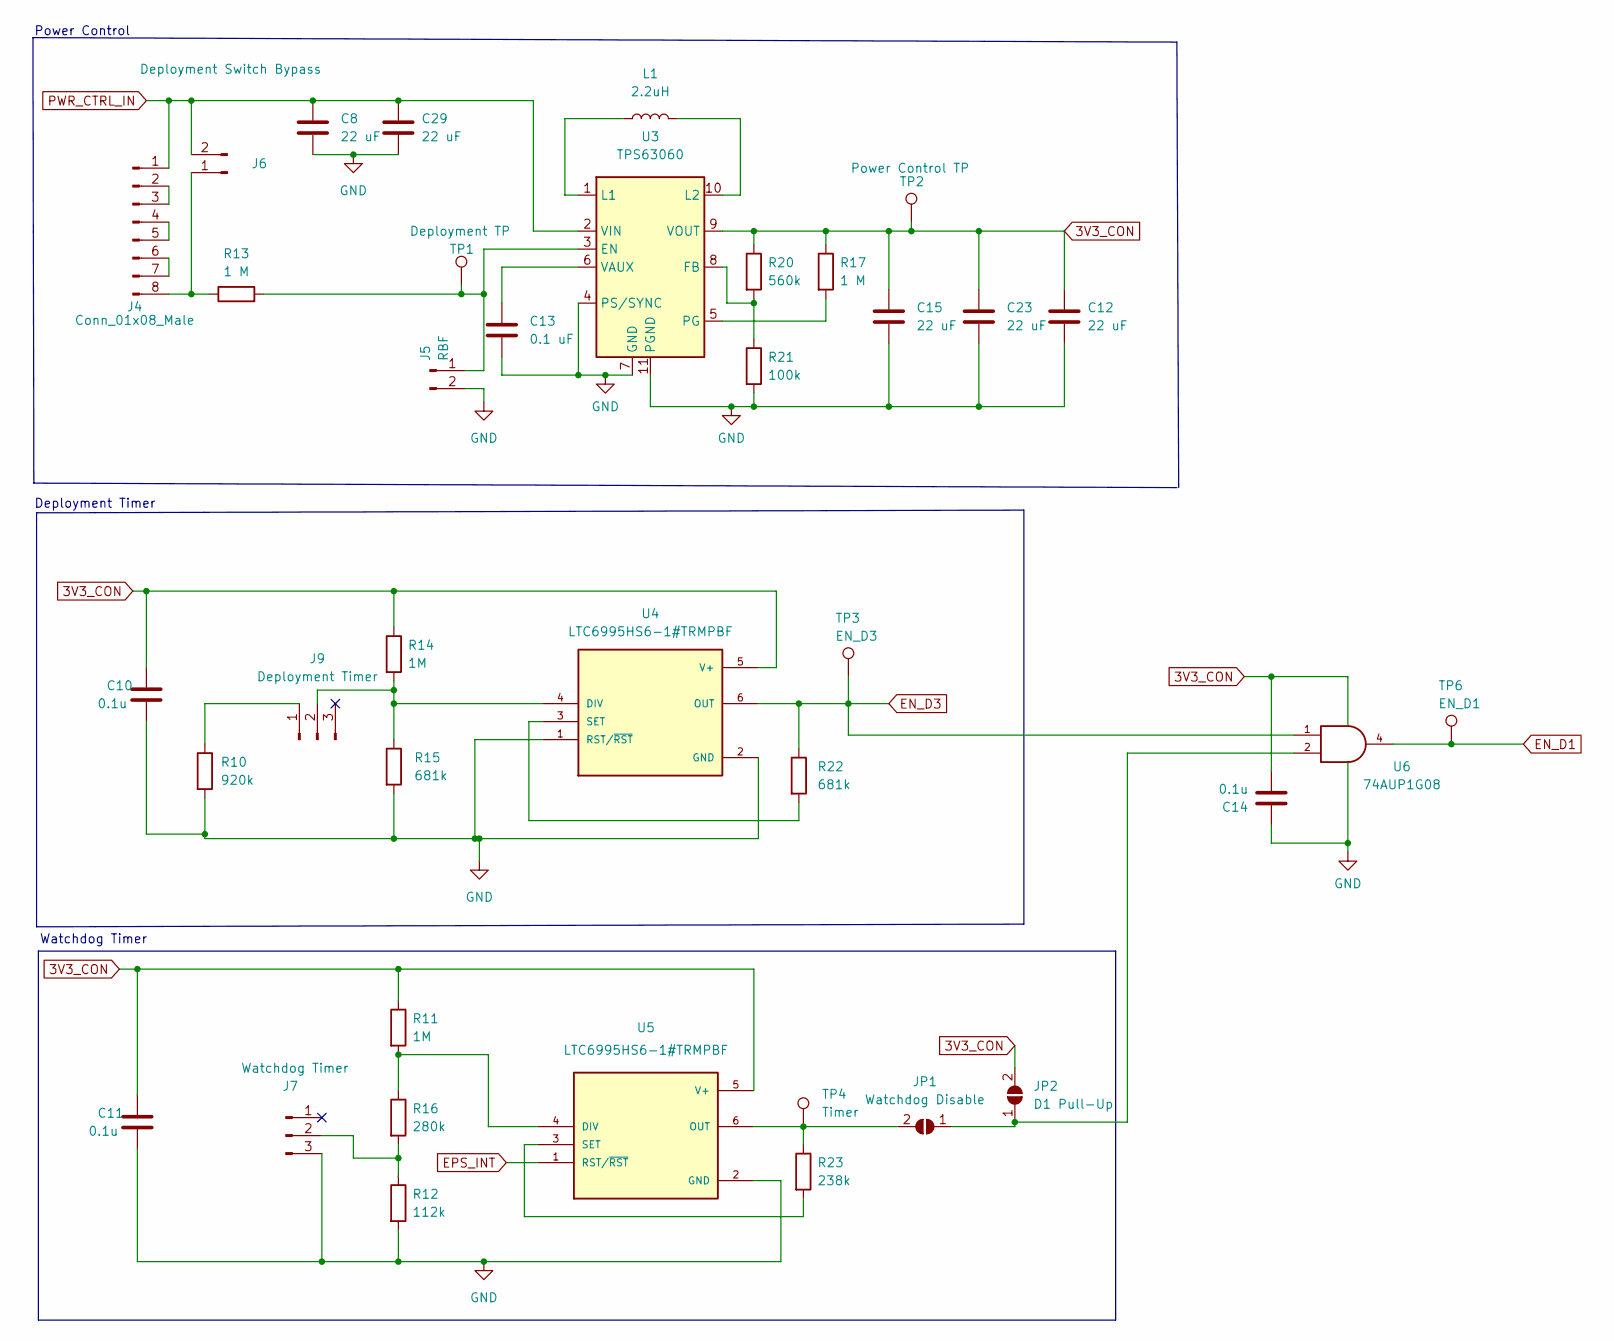
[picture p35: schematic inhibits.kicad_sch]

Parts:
C8, C12, C15, C23, C29: 22 uF; C_0402_1005Metric
C10, C11: 0.1u; C_0402_1005Metric
C13: 0.1 uF; C_0402_1005Metric
C14: 0.1u; C_0603_1608Metric
J4: Conn_01x08_Male; M80-5300842
J5: RBF; PinHeader_1x02_P2.00mm_Horizontal
J6: Deployment Switch Bypass; PinHeader_1x02_P2.00mm_Horizontal
J7: Watchdog Timer; PinHeader_1x03_P2.00mm_Horizontal
J9: Deployment Timer; PinHeader_1x03_P2.00mm_Horizontal
JP1: Watchdog Disable; SolderJumper-2_P1.3mm_Open_Pad1.0x1.5mm
JP2: D1 Pull-Up; SolderJumper-2_P1.3mm_Open_Pad1.0x1.5mm
L1: 2.2uH; L_0805_2012Metric_Pad1.15x1.40mm_HandSolder
R10: 920k; R_0402_1005Metric
R11, R14: 1M; R_0402_1005Metric
R12: 112k; R_0402_1005Metric
R13: 1 M; R_0603_1608Metric
R15, R22: 681k; R_0402_1005Metric
R16: 280k; R_0402_1005Metric
R17: 1 M; R_0402_1005Metric
R20: 560k; R_0402_1005Metric
R21: 100k; R_0402_1005Metric
R23: 238k; R_0402_1005Metric
TP1: Deployment TP; TestPoint_THTPad_D2.0mm_Drill1.0mm
TP2: Power Control TP; TestPoint_THTPad_D2.0mm_Drill1.0mm
TP3: EN_D3; TestPoint_THTPad_D2.0mm_Drill1.0mm
TP4: Timer; TestPoint_THTPad_D2.0mm_Drill1.0mm
TP6: EN_D1; TestPoint_THTPad_D2.0mm_Drill1.0mm
U3: TPS63060; Texas_S-PWSON-N10_ThermalVias
U4, U5: LTC6995HS6-1#TRMPBF; DFN-6_DCB_LIT; PARTREV Rev. B
U6: 74AUP1G08; SOT-353_SC-70-5_Handsoldering

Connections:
3V3_CON: C10.1, C11.1, C12.1, C14.2, C15.1, C23.1, JP2.2 (B), R11.1, R14.1, R17.1, R20.1, TP2.1, U3.9 (VOUT), U4.5 (V+), U5.5 (V+), U6.5 (VCC)
BCR_OUT: C8.1, C29.1, J4.1, J6.2, U3.2 (VIN); also elsewhere on the board
EN_D1: TP6.1, U6.4; also elsewhere on the board
EN_D3: R22.1, TP3.1, U4.6 (OUT), U6.1; also elsewhere on the board
EPS_INT: U5.1 (RST/~RST); also elsewhere on the board
GND: C8.2, C10.2, C11.2, C12.2, C13.2, C14.1, C15.2, C23.2, C29.2, J5.2, J7.3, R10.2, R12.2, R15.2, R21.2, U3.4 (PS/SYNC), U3.7 (GND), U3.11 (PGND), U4.1 (RST/~RST), U4.2 (GND), U5.2 (GND), U6.3 (GND); also elsewhere on the board
unnamed: C13.1, U3.6 (VAUX)
unnamed: J4.2, J4.3
unnamed: J4.4, J4.5
unnamed: J4.6, J4.7
unnamed: J4.8, J6.1, R13.1
unnamed: J5.1, R13.2, TP1.1, U3.3 (EN)
unnamed: J7.2, R12.1, R16.2
unnamed: J9.1, R10.1
unnamed: J9.2, R14.2, R15.1, U4.4 (DIV)
unnamed: JP1.1 (A), JP2.1 (A), U6.2
unnamed: JP1.2 (B), R23.1, TP4.1, U5.6 (OUT)
unnamed: L1.1, U3.1 (L1)
unnamed: L1.2, U3.10 (L2)
unnamed: R11.2, R16.1, U5.4 (DIV)
unnamed: R17.2, U3.5 (PG)
unnamed: R20.2, R21.1, U3.8 (FB)
unnamed: R22.2, U4.3 (SET)
unnamed: R23.2, U5.3 (SET)

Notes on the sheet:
Deployment Timer
Watchdog Timer
Power Control

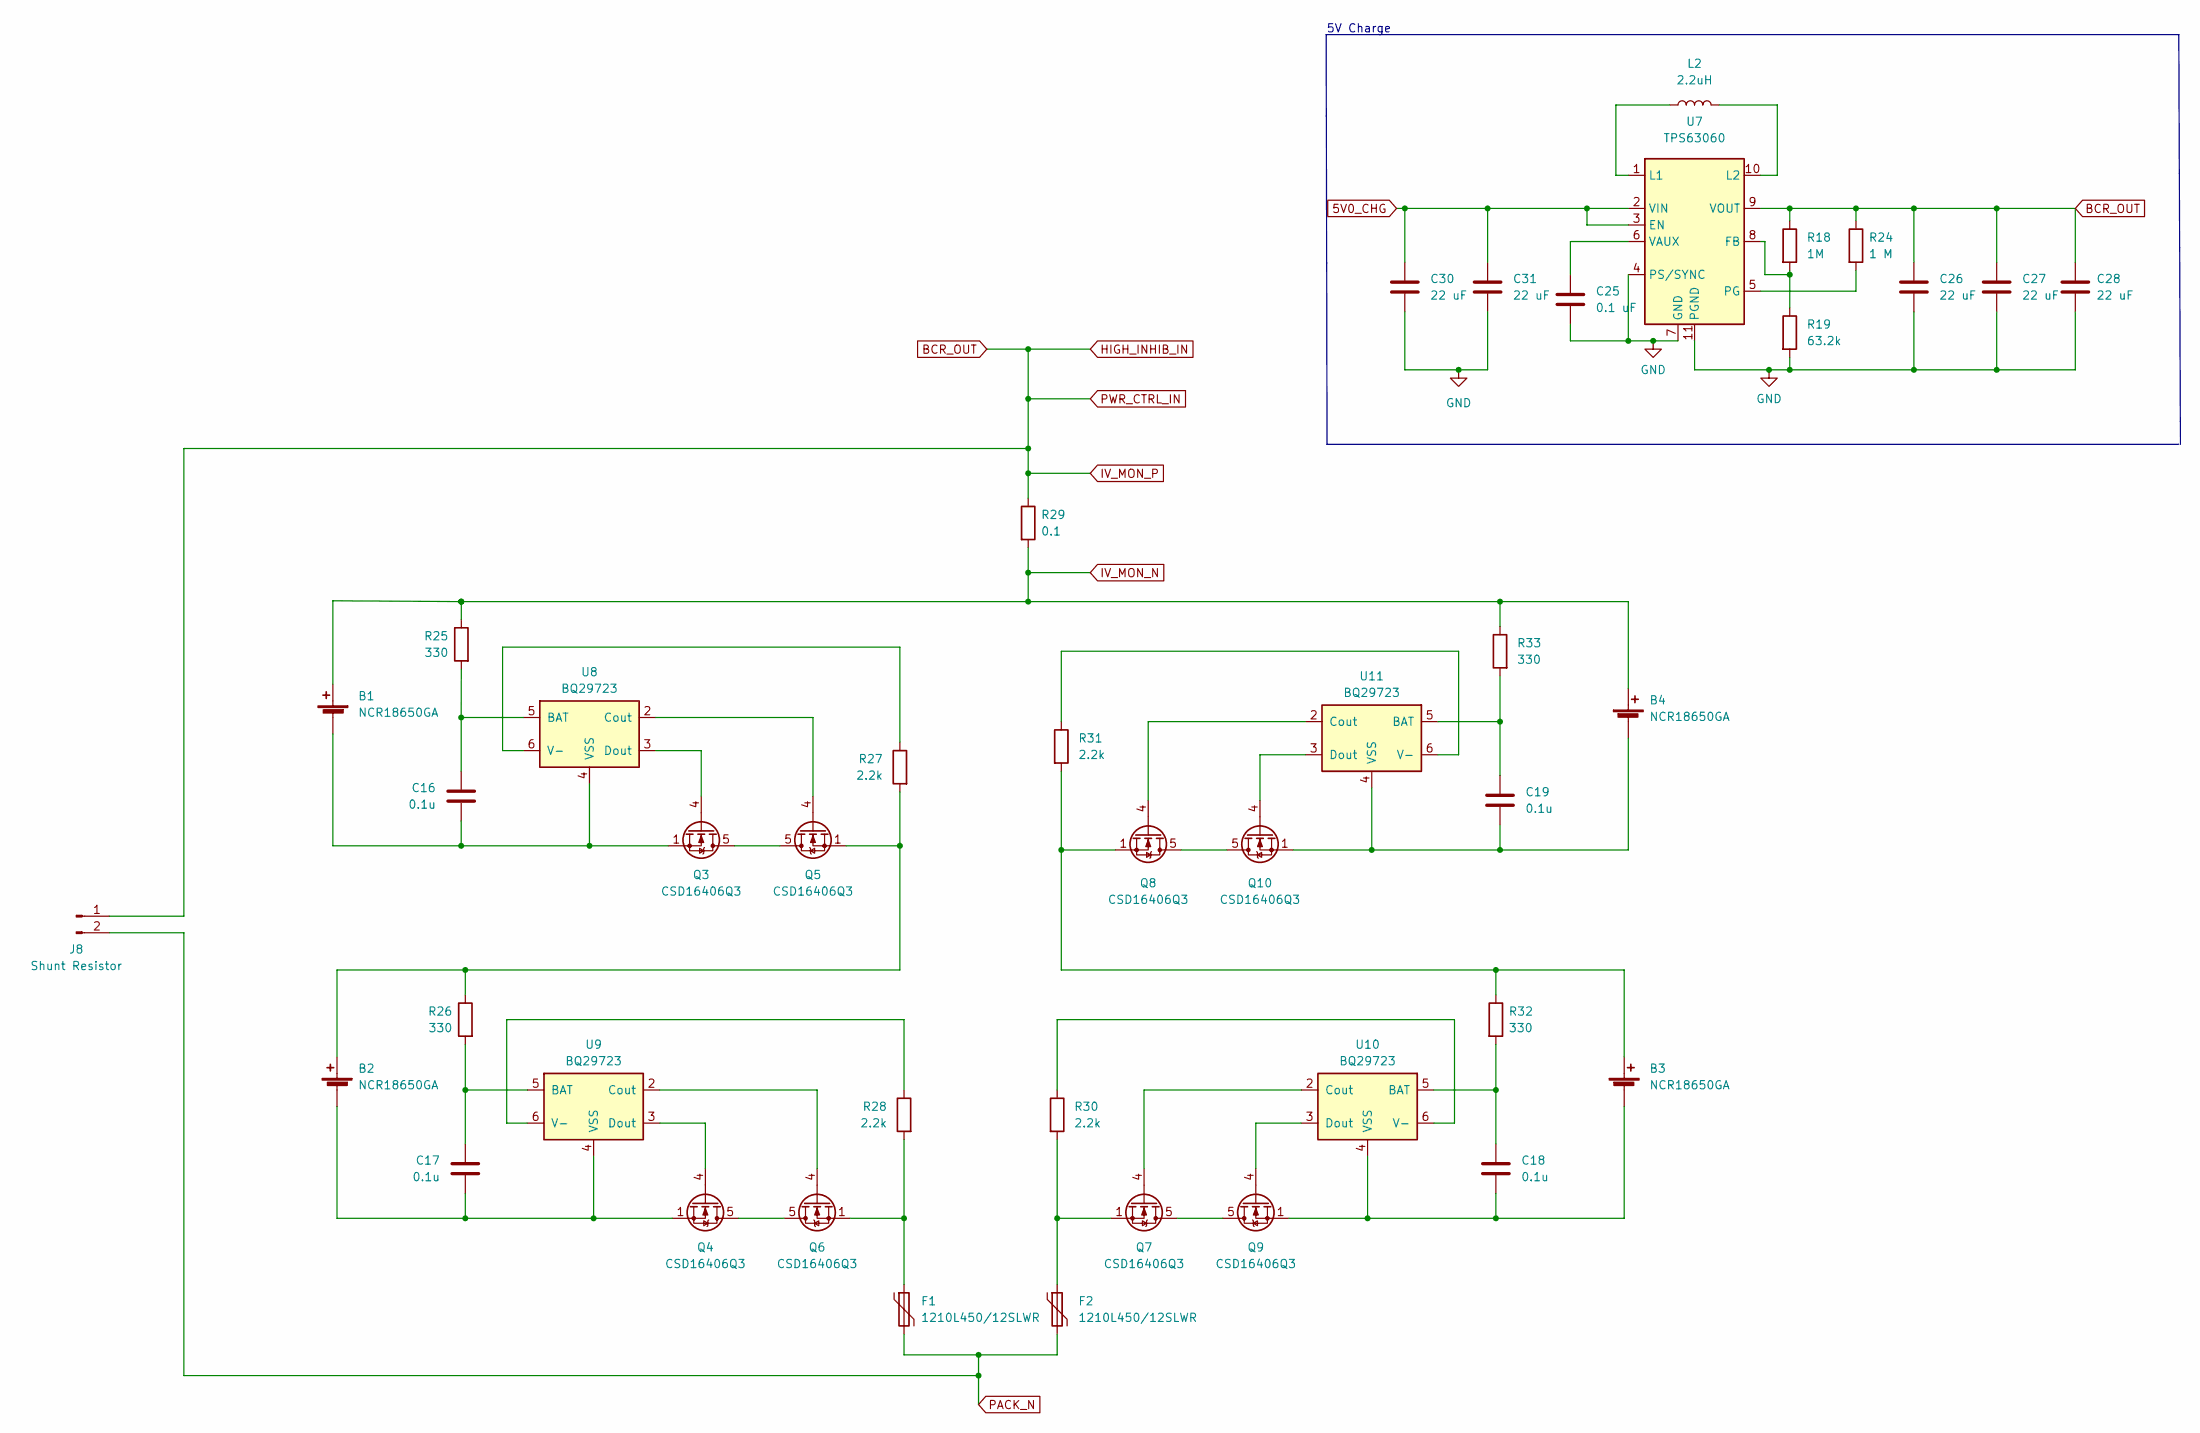
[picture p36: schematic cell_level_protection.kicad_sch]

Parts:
B1, B2, B3, B4: NCR18650GA; Keystone_54_18650
C16, C17, C18, C19: 0.1u; C_0603_1608Metric
C25: 0.1 uF; C_0603_1608Metric
C26, C27, C28, C30, C31: 22 uF; C_0603_1608Metric
F1, F2: 1210L450/12SLWR; 1210L450-polyfuse
J8: Shunt Resistor; PinHeader_1x02_P2.00mm_Vertical
L2: 2.2uH; L_0805_2012Metric_Pad1.15x1.40mm_HandSolder
Q3, Q4, Q5, Q6, Q7, Q8, Q9, Q10: CSD16406Q3; TDSON-8-1
R18: 1M; R_0603_1608Metric
R19: 63.2k; R_0603_1608Metric
R24: 1 M; R_0603_1608Metric
R25, R26, R32, R33: 330; R_0603_1608Metric
R27, R28, R30, R31: 2.2k; R_0603_1608Metric
R29: 0.1; R_0603_1608Metric
U7: TPS63060; Texas_S-PWSON-N10_ThermalVias
U8, U9, U10, U11: BQ29723; WSON-6_1.5x1.5mm_P0.5mm

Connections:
5V0_CHG: C30.1, C31.1, U7.2 (VIN), U7.3 (EN); also elsewhere on the board
BCR_OUT: C26.1, C27.1, C28.1, J8.1, R18.1, R24.1, R29.1, U7.9 (VOUT); also elsewhere on the board
GND: C25.2, C26.2, C27.2, C28.2, C30.2, C31.2, R19.2, U7.4 (PS/SYNC), U7.7 (GND), U7.11 (PGND); also elsewhere on the board
IV_MON_N: B1.1 (+), B4.1 (+), R25.1, R29.2, R33.1; also elsewhere on the board
unnamed: B1.2 (-), C16.1, Q3.1 (S), Q3.2 (S), Q3.3 (S), U8.4 (VSS)
unnamed: B2.1 (+), Q5.1 (S), Q5.2 (S), Q5.3 (S), R26.1, R27.2
unnamed: B2.2 (-), C17.1, Q4.1 (S), Q4.2 (S), Q4.3 (S), U9.4 (VSS)
unnamed: B3.1 (+), Q8.1 (S), Q8.2 (S), Q8.3 (S), R31.2, R32.1
unnamed: B3.2 (-), C18.1, Q9.1 (S), Q9.2 (S), Q9.3 (S), U10.4 (VSS)
unnamed: B4.2 (-), C19.1, Q10.1 (S), Q10.2 (S), Q10.3 (S), U11.4 (VSS)
unnamed: C16.2, R25.2, U8.5 (BAT)
unnamed: C17.2, R26.2, U9.5 (BAT)
unnamed: C18.2, R32.2, U10.5 (BAT)
unnamed: C19.2, R33.2, U11.5 (BAT)
unnamed: C25.1, U7.6 (VAUX)
unnamed: F1.1, Q6.1 (S), Q6.2 (S), Q6.3 (S), R28.2
unnamed: F2.1, Q7.1 (S), Q7.2 (S), Q7.3 (S), R30.2
unnamed: L2.1, U7.1 (L1)
unnamed: L2.2, U7.10 (L2)
unnamed: Q3.4 (G), U8.3 (Dout)
unnamed: Q3.5 (D), Q5.5 (D)
unnamed: Q4.4 (G), U9.3 (Dout)
unnamed: Q4.5 (D), Q6.5 (D)
unnamed: Q5.4 (G), U8.2 (Cout)
unnamed: Q6.4 (G), U9.2 (Cout)
unnamed: Q7.4 (G), U10.2 (Cout)
unnamed: Q7.5 (D), Q9.5 (D)
unnamed: Q8.4 (G), U11.2 (Cout)
unnamed: Q9.4 (G), U10.3 (Dout)
unnamed: Q10.4 (G), U11.3 (Dout)
unnamed: Q8.5 (D), Q10.5 (D)
unnamed: R18.2, R19.1, U7.8 (FB)
unnamed: R24.2, U7.5 (PG)
unnamed: R27.1, U8.6 (V-)
unnamed: R28.1, U9.6 (V-)
unnamed: R30.1, U10.6 (V-)
unnamed: R31.1, U11.6 (V-)
PACK_N: F1.2, F2.2, J8.2; also elsewhere on the board

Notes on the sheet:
5V Charge

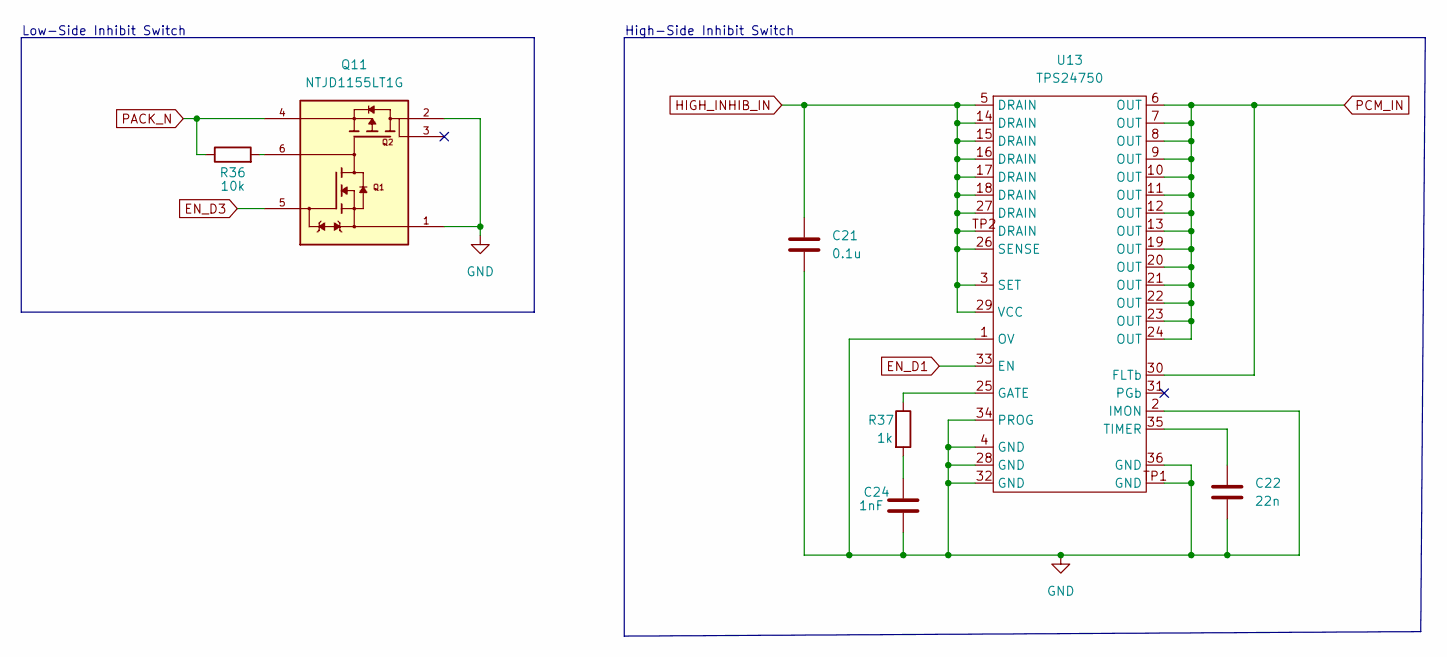
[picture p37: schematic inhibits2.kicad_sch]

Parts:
C21: 0.1u; C_0402_1005Metric
C22: 22n; C_0402_1005Metric
C24: 1nF; C_0402_1005Metric
Q11: NTJD1155LT1G; TRANS_NTJD1155LT1G; PARTREV Rev. 6
R36: 10k; R_0402_1005Metric
R37: 1k; R_0402_1005Metric
U13: TPS24750

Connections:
BCR_OUT: C21.1, U13.3 (SET), U13.5 (DRAIN), U13.14 (DRAIN), U13.15 (DRAIN), U13.16 (DRAIN), U13.17 (DRAIN), U13.18 (DRAIN), U13.26 (SENSE), U13.27 (DRAIN), U13.29 (VCC), U13.TP2 (DRAIN); also elsewhere on the board
EN_D1: U13.33 (EN); also elsewhere on the board
EN_D3: Q11.5; also elsewhere on the board
GND: C21.2, C22.2, C24.2, Q11.1, Q11.2, U13.1 (OV), U13.2 (IMON), U13.4 (GND), U13.28 (GND), U13.32 (GND), U13.34 (PROG), U13.36 (GND), U13.TP1 (GND); also elsewhere on the board
unnamed: C22.1, U13.35 (TIMER)
unnamed: C24.1, R37.2
unnamed: Q11.6, R36.2
unnamed: R37.1, U13.25 (GATE)
PACK_N: Q11.4, R36.1; also elsewhere on the board
PCM_IN: U13.6 (OUT), U13.7 (OUT), U13.8 (OUT), U13.9 (OUT), U13.10 (OUT), U13.11 (OUT), U13.12 (OUT), U13.13 (OUT), U13.19 (OUT), U13.20 (OUT), U13.21 (OUT), U13.22 (OUT), U13.23 (OUT), U13.24 (OUT), U13.30 (FLTb); also elsewhere on the board

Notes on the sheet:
Low-Side Inhibit Switch
High-Side Inhibit Switch

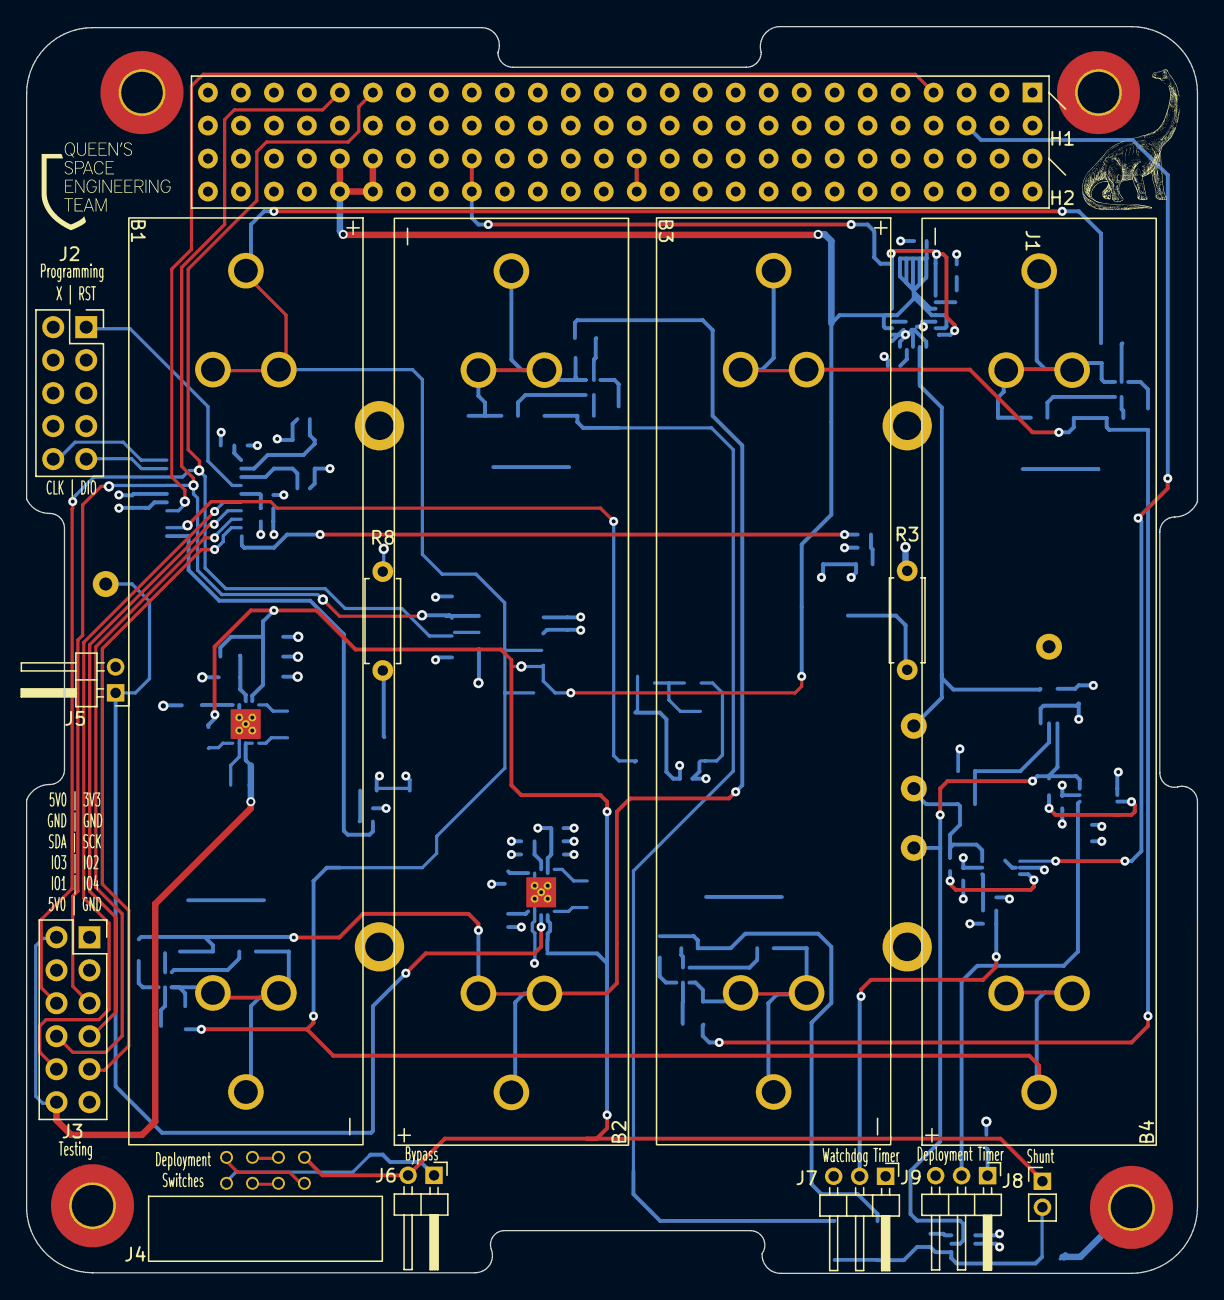
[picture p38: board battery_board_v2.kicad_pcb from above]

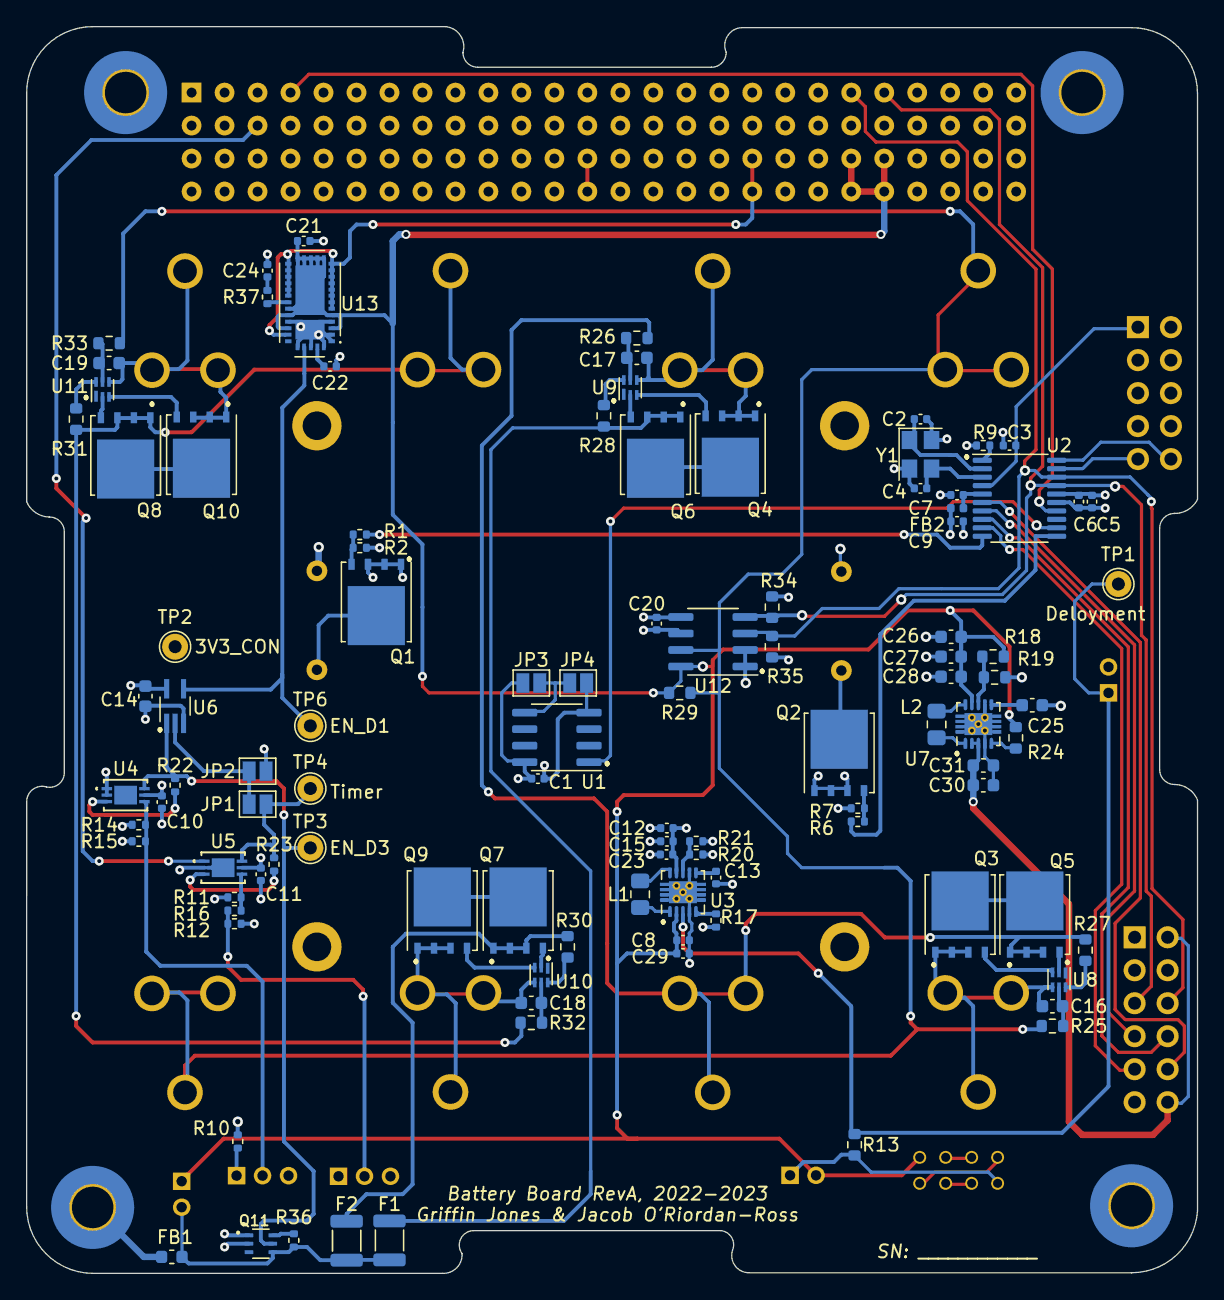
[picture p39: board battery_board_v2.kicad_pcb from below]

Board: 4 copper layers, 90.2 x 96.0 mm, 127 parts (104 on the bottom side), 90 nets.

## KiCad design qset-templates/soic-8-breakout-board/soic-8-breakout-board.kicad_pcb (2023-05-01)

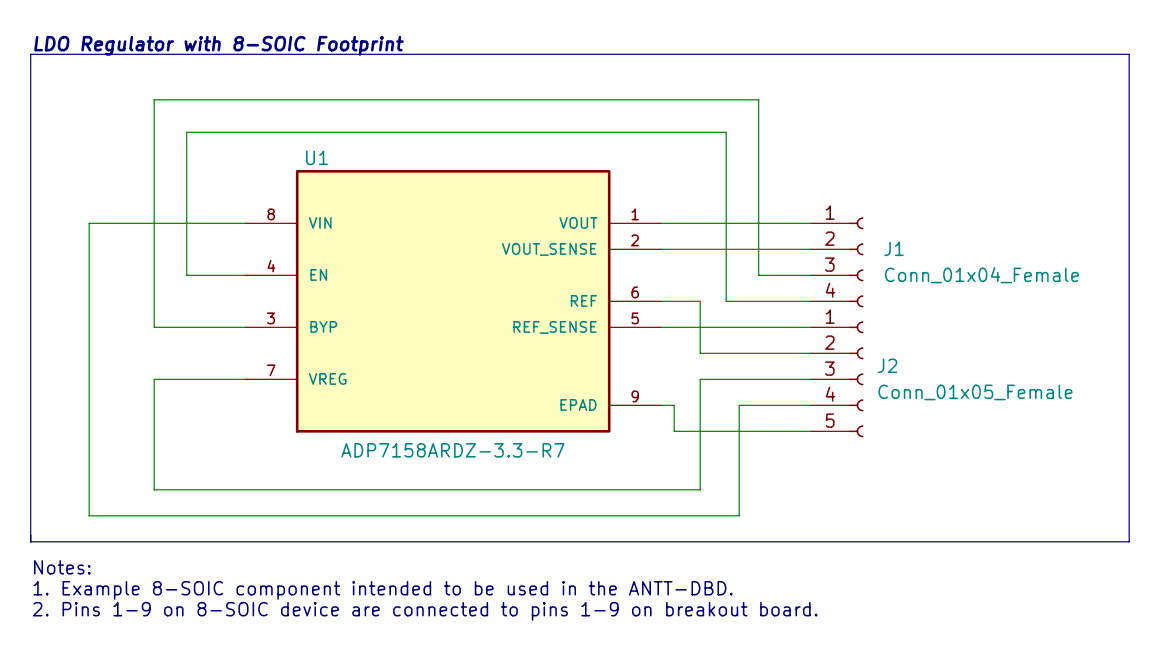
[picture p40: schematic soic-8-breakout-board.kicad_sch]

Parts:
J1: Conn_01x04_Female; PinSocket_1x04_P2.54mm_Vertical
J2: Conn_01x05_Female; PinSocket_1x05_P2.54mm_Vertical
U1: ADP7158ARDZ-3.3-R7; SOIC127P600X175-9N; PARTREV C

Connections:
unnamed: J1.1, U1.1 (VOUT)
unnamed: J1.2, U1.2 (VOUT_SENSE)
unnamed: J1.3, U1.3 (BYP)
unnamed: J1.4, U1.4 (EN)
unnamed: J2.1, U1.5 (REF_SENSE)
unnamed: J2.2, U1.6 (REF)
unnamed: J2.3, U1.7 (VREG)
unnamed: J2.4, U1.8 (VIN)
unnamed: J2.5, U1.9 (EPAD)

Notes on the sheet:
LDO Regulator with 8-SOIC Footprint
Notes: 1. Example 8-SOIC component intended to be used in the ANTT-DBD. 2. Pins 1-9 on 8-SOIC device are connected to pins 1-9 on breakout board.

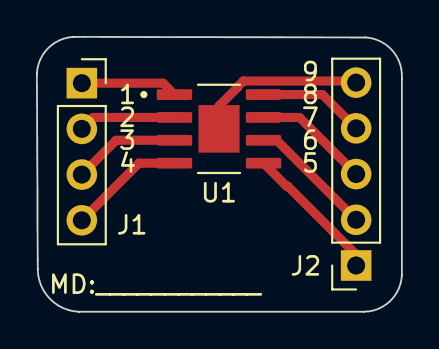
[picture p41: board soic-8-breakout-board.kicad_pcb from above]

Board: 2 copper layers, 20.3 x 15.3 mm, 3 parts (0 on the bottom side), 9 nets.

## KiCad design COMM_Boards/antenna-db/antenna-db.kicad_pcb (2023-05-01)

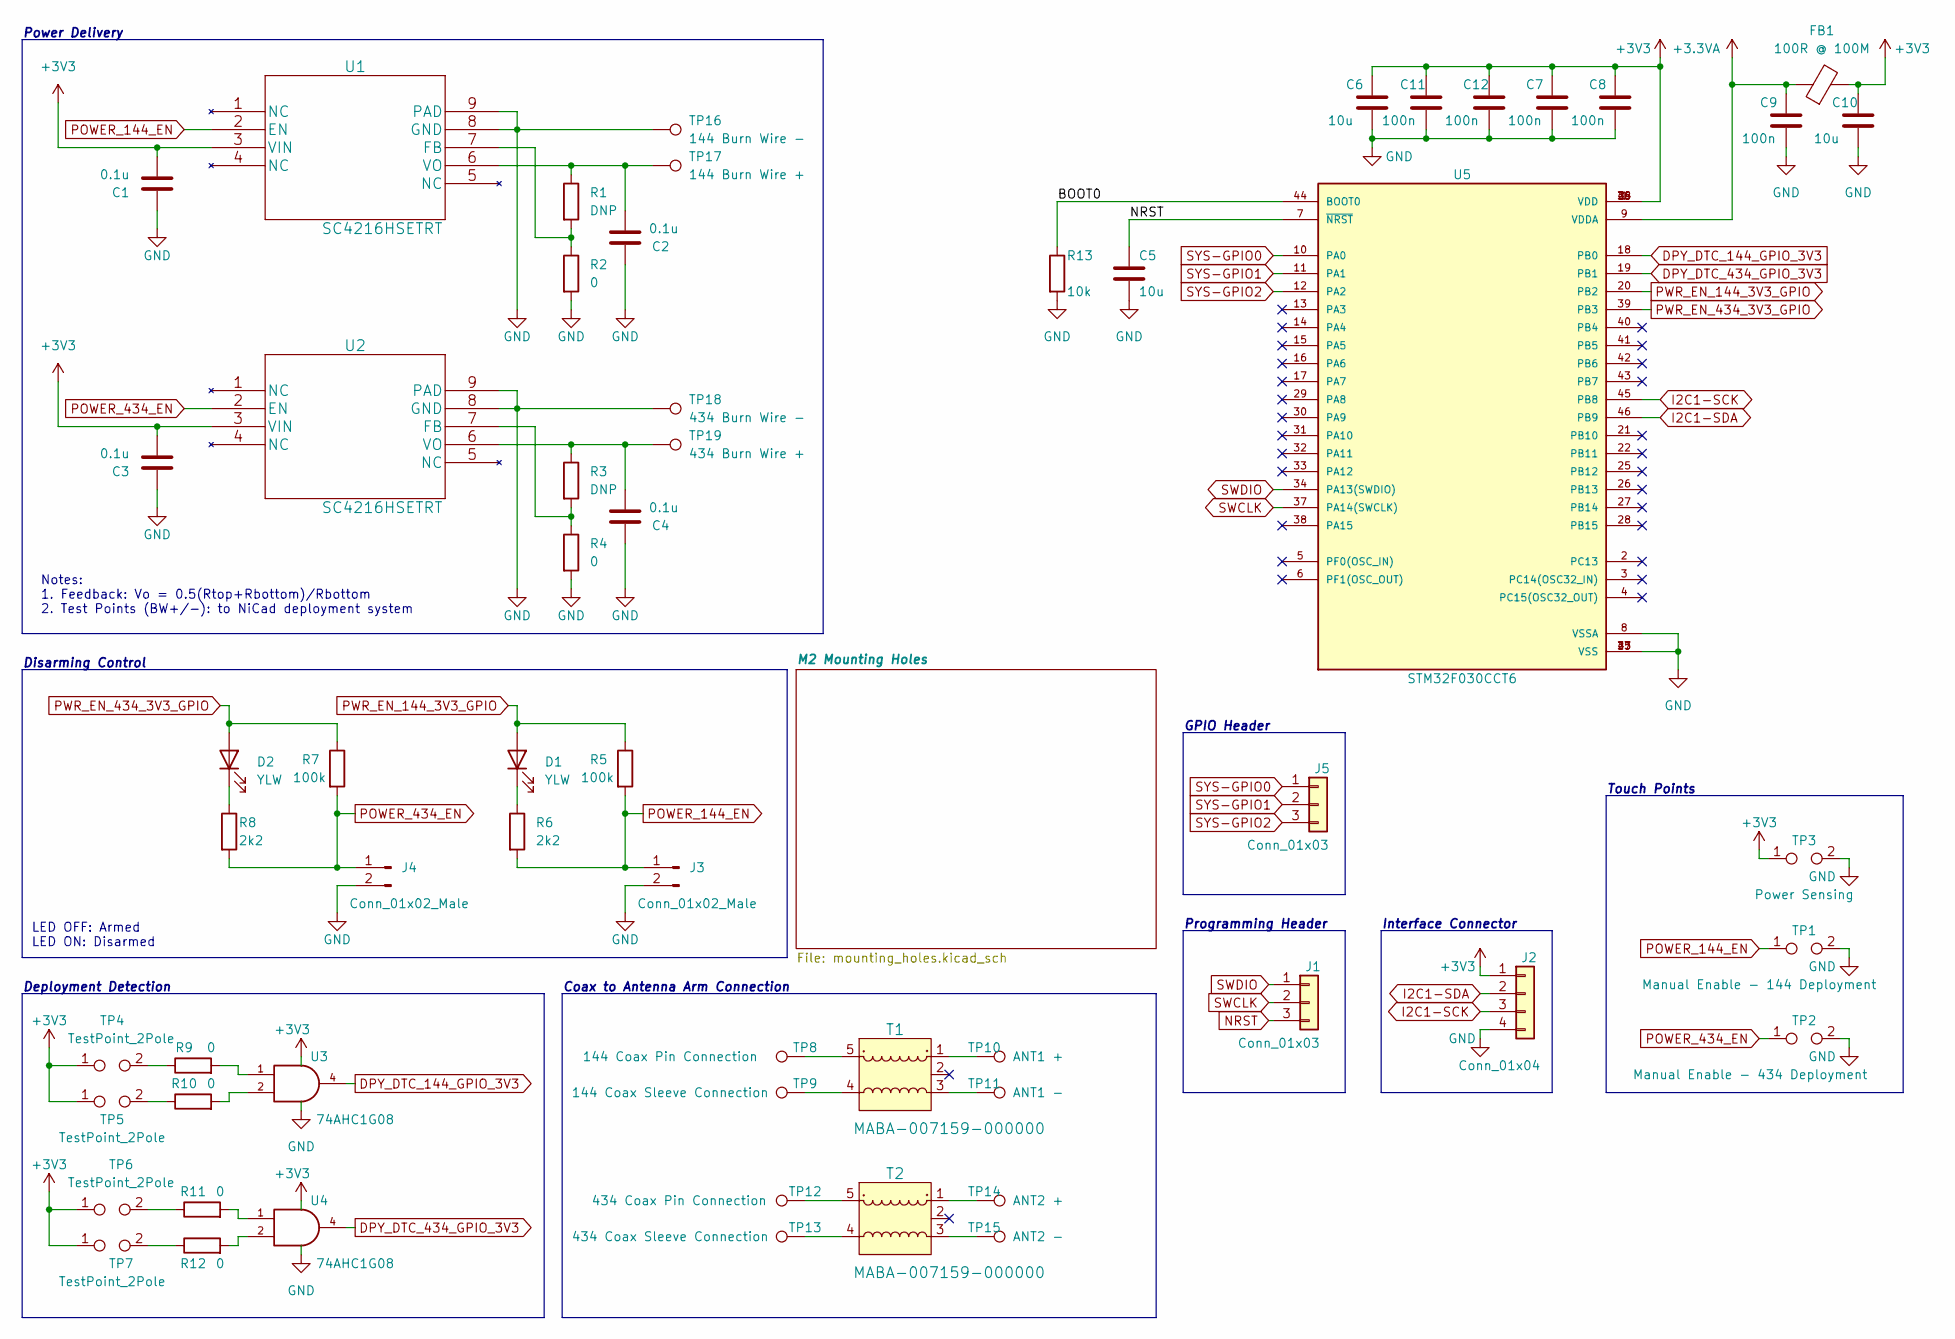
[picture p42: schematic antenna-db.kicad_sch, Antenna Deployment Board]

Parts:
C1, C2, C3, C4: 0.1u; C_0603_1608Metric
C5, C6, C10: 10u; C_0603_1608Metric
C7, C8, C9, C11, C12: 100n; C_0603_1608Metric
D1, D2: YLW; LED_0603_1608Metric
FB1: 100R @ 100M; L_0603_1608Metric
J1, J5: Conn_01x03; SAMTEC_TSM-103-01-L-SH
J2: Conn_01x04; SAMTEC_TSM-104-01-L-SH
J3, J4: Conn_01x02_Male; SAMTEC_TSM-102-01-L-SH
R1, R3: DNP; R_0603_1608Metric_Pad0.98x0.95mm_HandSolder
R2, R4: 0; R_0603_1608Metric_Pad0.98x0.95mm_HandSolder
R5, R7: 100k; R_0603_1608Metric
R6, R8: 2k2; R_0603_1608Metric
R9, R10, R11, R12: 0; R_0603_1608Metric
R13: 10k; R_0603_1608Metric
T1, T2: MABA-007159-000000; MPN MABA-007159-000000; Digi-Key_PN 1465-1302-1-ND
TP1: Manual Enable - 144 Deployment; TestPoint_2Pads_Pitch2.54mm_Drill0.8mm
TP2: Manual Enable - 434 Deployment; TestPoint_2Pads_Pitch2.54mm_Drill0.8mm
TP3: Power Sensing; TestPoint_2Pads_Pitch2.54mm_Drill0.8mm
TP4, TP5, TP6, TP7: TestPoint_2Pole; TestPoint_2Pads_Pitch2.54mm_Drill0.8mm
TP8: 144 Coax Pin Connection; TestPoint_THTPad_2.0x2.0mm_Drill1.0mm
TP9: 144 Coax Sleeve Connection; TestPoint_THTPad_2.0x2.0mm_Drill1.0mm
TP10: ANT1 +; TestPoint_THTPad_4.0x4.0mm_Drill2.0mm
TP11: ANT1 -; TestPoint_THTPad_4.0x4.0mm_Drill2.0mm
TP12: 434 Coax Pin Connection; TestPoint_THTPad_2.0x2.0mm_Drill1.0mm
TP13: 434 Coax Sleeve Connection; TestPoint_THTPad_2.0x2.0mm_Drill1.0mm
TP14: ANT2 +; TestPoint_THTPad_4.0x4.0mm_Drill2.0mm
TP15: ANT2 -; TestPoint_THTPad_4.0x4.0mm_Drill2.0mm
TP16: 144 Burn Wire -; TestPoint_THTPad_2.0x2.0mm_Drill1.0mm
TP17: 144 Burn Wire +; TestPoint_THTPad_2.0x2.0mm_Drill1.0mm
TP18: 434 Burn Wire -; TestPoint_THTPad_2.0x2.0mm_Drill1.0mm
TP19: 434 Burn Wire +; TestPoint_THTPad_2.0x2.0mm_Drill1.0mm
U1, U2: SC4216HSETRT; SOIC-8-1EP_3.9x4.9mm_P1.27mm_EP2.29x3mm
U3, U4: 74AHC1G08; SOT-353_SC-70-5
U5: STM32F030CCT6; QFP50P900X900X160-48N

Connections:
+3.3VA: C9.1, FB1.1, U5.9 (VDDA)
+3V3: C1.2, C3.2, C6.1, C7.1, C8.1, C10.1, C11.1, C12.1, FB1.2, J2.1, TP3.1, TP4.1, TP5.1, TP6.1, TP7.1, U1.3 (VIN), U2.3 (VIN), U3.5 (VCC), U4.5 (VCC), U5.1 (VDD), U5.24 (VDD), U5.36 (VDD), U5.48 (VDD)
/BOOT0: R13.1, U5.44 (BOOT0)
DPY_DTC_144_GPIO_3V3: U3.4, U5.18 (PB0)
DPY_DTC_434_GPIO_3V3: U4.4, U5.19 (PB1)
GND: C1.1, C2.1, C3.1, C4.1, C5.2, C6.2, C7.2, C8.2, C9.2, C10.2, C11.2, C12.2, J2.4, J3.2, J4.2, R2.2, R4.2, R13.2, TP1.2, TP2.2, TP3.2, TP16.1, TP18.1, U1.8 (GND), U1.9 (PAD), U2.8 (GND), U2.9 (PAD), U3.3 (GND), U4.3 (GND), U5.8 (VSSA), U5.23 (VSS), U5.35 (VSS), U5.47 (VSS)
I2C1-SCK: J2.3, U5.45 (PB8)
I2C1-SDA: J2.2, U5.46 (PB9)
NRST: C5.1, J1.3, U5.7 (~NRST)
unnamed: C2.2, R1.1, TP17.1, U1.6 (VO)
unnamed: C4.2, R3.1, TP19.1, U2.6 (VO)
unnamed: D1.1 (K), R6.1
unnamed: D2.1 (K), R8.1
unnamed: R1.2, R2.1, U1.7 (FB)
unnamed: R3.2, R4.1, U2.7 (FB)
unnamed: R9.1, TP4.2
unnamed: R10.1, TP5.2
unnamed: R11.1, TP6.2
unnamed: R12.1, TP7.2
unnamed: T1.1, TP10.1
unnamed: T1.3, TP11.1
unnamed: T1.4, TP9.1
unnamed: T1.5, TP8.1
unnamed: T2.1, TP14.1
unnamed: T2.3, TP15.1
unnamed: T2.4, TP13.1
unnamed: T2.5, TP12.1
unnamed: R9.2, U3.1
unnamed: R10.2, U3.2
unnamed: R11.2, U4.1
unnamed: R12.2, U4.2
POWER_144_EN: J3.1, R5.2, R6.2, TP1.1, U1.2 (EN)
POWER_434_EN: J4.1, R7.2, R8.2, TP2.1, U2.2 (EN)
PWR_EN_144_3V3_GPIO: D1.2 (A), R5.1, U5.20 (PB2)
PWR_EN_434_3V3_GPIO: D2.2 (A), R7.1, U5.39 (PB3)
SWCLK: J1.2, U5.37 (PA14(SWCLK))
SWDIO: J1.1, U5.34 (PA13(SWDIO))
SYS-GPIO0: J5.1, U5.10 (PA0)
SYS-GPIO1: J5.2, U5.11 (PA1)
SYS-GPIO2: J5.3, U5.12 (PA2)

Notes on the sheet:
Power Delivery
Deployment Detection
Notes: 1. Feedback: Vo = 0.5(Rtop+Rbottom)/Rbottom 2. Test Points (BW+/-): to NiCad deployment system
LED OFF: Armed LED ON: Disarmed
Touch Points
GPIO Header
Coax to Antenna Arm Connection
Interface Connector
Disarming Control
Programming Header

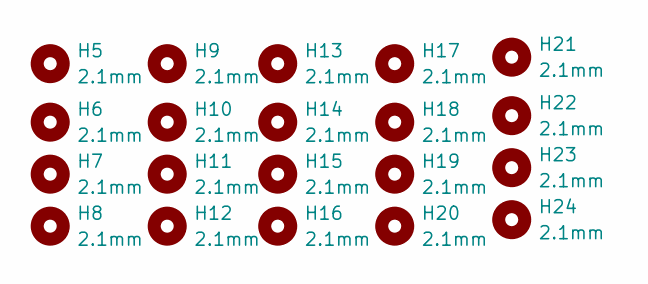
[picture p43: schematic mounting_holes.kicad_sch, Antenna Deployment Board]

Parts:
H5, H6, H7, H8, H9, H10, H11, H12, H13, H14, H15, H16, H17, H18, H19, H20, H21, H22, H23, H24: 2.1mm; MountingHole_2.2mm_M2_Pad_TopBottom


Board: 4 copper layers, 94.0 x 94.0 mm, 79 parts (0 on the bottom side), 40 nets.

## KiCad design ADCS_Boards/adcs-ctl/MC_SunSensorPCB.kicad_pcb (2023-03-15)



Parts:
C1, C17, C22, C23, C24, C43: 100nF; C_0603_1608Metric
C2, C6, C9, C16: 10uF; C_0603_1608Metric
C3, C4, C5, C7, C8: 100nF; C_0402_1005Metric
C10, C13: 4pF; C_0402_1005Metric
C11: 10nF; C_0402_1005Metric
C12, C14: 1uF; C_0603_1608Metric
C15, C37, C38: 1.0uF; C_0603_1608Metric
C18, C19, C20, C21, C25, C26, C27, C28, C29, C30, C31, C32, C33, C34, C35, C36: 180pF; C_0603_1608Metric
C39, C40, C41, C42: 0.1uF; C_0603_1608Metric
D1, D2, D3: GREEN; LED_0603_1608Metric
FB1: FerriteBead; L_0603_1608Metric
FB2: 100R @ 100 MHz; L_0603_1608Metric
H1, H2, H3, H4: MountingHole_Pad; MountingHole_3.2mm_M3_Pad_TopBottom
J1: PC104_Connector; pc104-connector
J2: Conn_02x06_Odd_Even; PinSocket_2x06_P2.54mm_Horizontal
J3: Conn_01x03_Female; PinHeader_1x03_P2.54mm_Vertical
Q1, Q2: RE1C002UNTCL
R1: 10k; R_0603_1608Metric
R2, R26: 2k2; R_0603_1608Metric
R3: 1Meg; R_0603_1608Metric
R4: 2Meg; R_0603_1608Metric
R5: 1k; R_0603_1608Metric
R6, R7, R8, R9, R12, R13, R14, R15, R16, R17, R18, R19, R20, R21, R22, R23: 5.76k; R_0603_1608Metric
R10, R11, R24, R25: 2.2k; R_0603_1608Metric
R27, R28: 10k; R_0402_1005Metric
S1: TL3305CF260QG; SW_TL3305CF260QG; PARTREV C
SW1: SW_SPDT; SW_SPDT_PCM12
TP1: GND; TestPoint_THTPad_2.0x2.0mm_Drill1.0mm
TP2: 1V8; TestPoint_THTPad_2.0x2.0mm_Drill1.0mm
TP3: 3V3; TestPoint_THTPad_2.0x2.0mm_Drill1.0mm
TP4: 5V0; TestPoint_THTPad_2.0x2.0mm_Drill1.0mm
U1: STM32F103RET6; QFP50P1200X1200X160-64N
U2: AMS1117-3.3; SOT-223-3_TabPin2
U3: AMS1117-1.8; SOT-223-3_TabPin2
U4: LM358N; DIP794W45P254L959H508Q8
U5: CD74HC4067M96; SOIC127P1030X265-24N
U6, U7, U8, U9: LM324N; Op-Amp
U10, U11, U12, U13: DF13-7P-1.25DS(20); Hirose_DF13-07P-1.25DS_1x07_P1.25mm_Horizontal
U14, U15: 9DoF IMU; QFN24-3X3
U16: MR25H10MDF; SON65P300X300X95-8N
Y1: Crystal_GND24; Crystal_SMD_3225-4Pin_3.2x2.5mm

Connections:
1.8V: C16.1, C37.1, C38.1, C39.1, C40.1, D2.2 (A), Q1.1 (G), Q2.1 (G), R10.2, R24.2, TP2.1, U3.2 (VO), U14.8 (VDDIO), U14.13 (VDD), U15.8 (VDDIO), U15.9 (AD0/SDO), U15.13 (VDD)
5VUSB_CHG: J1.32 (H1-32), J2.12
+3.3VA: C11.1, C12.1, FB1.1, U1.13 (VDDA)
+5V: C6.1, C15.1, C17.1, C22.1, C23.1, C24.1, J1.65 (H2-13), J2.2, TP4.1, U2.3 (VI), U3.3 (VI), U4.8 (V+), U5.24 (VCC), U6.4, U7.4, U8.4, U9.4
/BOOT0: R1.2, U1.60 (BOOT0)
/NRST: C1.1, S1.1, S1.2, U1.7 (NRST); also elsewhere on the board
/SW_BOOT0: R1.1, SW1.2 (B)
ADCS_GPIO_3V3_SYS1: J2.7, U1.26 (PB0/ADC12_IN8/TIM3_CH3/TIM8_CH2N)
ADCS_GPIO_3V3_SYS2: J2.8, U1.27 (PB1/ADC12_IN9/TIM3_CH4/TIM8_CH3N)
ADCS_GPIO_3V3_SYS3: J2.9, U1.28 (PB2//BOOT1)
ADCS_GPIO_INT_OBC: J1.5 (H1-5), U1.33 (PB12/SPI2_NSS/I2S2_WS/I2C2_SMBA/USART3_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)
ADCS_GPIO_MRAM_HOLD: R27.2, U1.24 (PC4/ADC12_IN14), U16.7 (HOLD)
ADCS_GPIO_MRAM_WP: R28.1, U1.25 (PC5/ADC12_IN15), U16.3 (WP)
ADCS_GPIO_MTR_ENABLE: J1.42 (H1-42), U1.61 (PB8/TIM4_CH3/SDIO_D4/I2C1_SCL/CAN_RX)
ADCS_GPIO_MTR_XCOIL_CTL: J1.44 (H1-44), U1.62 (PB9/TIM4_CH4/SDIO_D5/I2C1_SDA/CAN_TX)
ADCS_GPIO_MTR_YCOIL_CTL: J1.45 (H1-45), U1.2 (PC13-TAMPER-RTC)
ADCS_GPIO_MTR_ZCOIL_CTL: J1.46 (H1-46), U1.3 (PC14-OSC32_IN)
ADCS_GPIO_RW1_DIR: J1.20 (H1-20), U1.38 (PC7/I2S3_MCK/TIM8_CH2/SDIO_D7/TIM3_CH2)
ADCS_GPIO_RW1_ENABLE: J1.16 (H1-16), U1.34 (PB13/SPI2_SCK/I2S2_CK/USART3_CTS/TIM1_C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)
ADCS_GPIO_RW1_PWM_SET: J1.24 (H1-24), U1.42 (PA9/USART1_TX/TIM1_CH2)
ADCS_GPIO_RW1_RAMP: J1.37 (H1-37), U1.51 (PC10/UART4_TX/SDIO_D2/USART3_TX)
ADCS_GPIO_RW2_DIR: J1.21 (H1-21), U1.39 (PC8/TIM8_CH3/SDIO_D0/TIM3_CH3)
ADCS_GPIO_RW2_ENABLE: J1.17 (H1-17), U1.35 (PB14/SPI2_MISO/TIM1_CH2N/USART3_RTS)
ADCS_GPIO_RW2_PWM_SET: J1.25 (H1-25), U1.43 (PA10/USART1_RX/TIM1_CH3)
ADCS_GPIO_RW2_RAMP: J1.38 (H1-38), U1.52 (PC11/UART4_RX/SDIO_D3/USART3_RX)
ADCS_GPIO_RW3_DIR: J1.22 (H1-22), U1.40 (PC9/TIM8_CH4/SDIO_D1/TIM3_CH4)
ADCS_GPIO_RW3_ENABLE: J1.18 (H1-18), U1.36 (PB15/SPI2_MOSI/I2S2_SD/TIM1_CH3N)
ADCS_GPIO_RW3_PWM_SET: J1.26 (H1-26), U1.44 (PA11/USART1_CTS/USBDMCAN_RX/TIM1_CH4)
ADCS_GPIO_RW3_RAMP: J1.39 (H1-39), U1.53 (PC12/UART5_TX/SDIO_CK/USART3_CK)
ADCS_GPIO_RW4_DIR: J1.23 (H1-23), U1.41 (PA8/USART1_CK/TIM1_CH1/MCO)
ADCS_GPIO_RW4_ENABLE: J1.19 (H1-19), U1.37 (PC6/I2S2_MCK/TIM8_CH1/SDIO_D6/TIM3_CH1)
ADCS_GPIO_RW4_PWM_SET: J1.27 (H1-27), U1.45 (PA12/USART1_RTS/USBDP/CAN_TX/TIM1_ETR)
ADCS_GPIO_RW4_RAMP: J1.40 (H1-40), U1.54 (PD2/TIM3_ETR/UART5_RX/SDIO_CMD)
ADCS_PWM_MTR_XCOIL_CTL: J1.47 (H1-47), U1.4 (PC15-OSC32_OUT)
ADCS_PWM_MTR_YCOIL_CTL: J1.48 (H1-48), U1.8 (PC0/ADC123_IN10)
ADCS_PWM_MTR_ZCOIL_CTL: J1.49 (H1-49), U1.9 (PC1/ADC123_IN11)
ADCS_SPI_MRAM_MISO: U1.22 (PA6/SPI1_MISO/TIM8_BKIN/ADC12_IN6/TIM3_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), U16.2 (SO)
ADCS_SPI_MRAM_MOSI: U1.23 (PA7/SPI1_MOSI/TIM8_CH1N/ADC12_IN7/TIM3_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), U16.5 (SI)
ADCS_SPI_MRAM_NSS: U1.20 (PA4/SPI1_NSS/USART2_CK/DAC_OUT1/ADC12_I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), U16.1 (CS)
ADCS_SPI_MRAM_SCK: U1.21 (PA5/SPI1_SCK/DAC_OUT2/ADC12_IN5), U16.6 (SCK)
ADCS_SPI_MTR_CSN: J1.50 (H1-50), U1.50 (PA15/SPI3_NSS/I2S3_WS)
ADCS_SPI_MTR_MISO: J1.36 (H1-36), U1.56 (PB4/SPI3_MISO/TIM3_CH1/SPI1_MISO)
ADCS_SPI_MTR_MOSI: J1.52 (H1-52), U1.57 (PB5/TIM3_CH2/SPI1_MOSI/)
ADCS_SPI_MTR_SCK: J1.51 (H1-51), U1.55 (PB3/SPI3_SCK/I2S3_CK/TRACESWO/TIM2_CH2/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)
GND: C1.2, C2.2, C3.2, C4.2, C5.2, C6.2, C7.2, C8.2, C9.1, C10.2, C11.2, C12.2, C13.2, C14.2, C15.2, C16.2, C17.2, C22.2, C23.2, C24.2, C37.2, C38.2, C39.2, C40.2, C41.2, C42.2, C43.2, J1.61 (H2-9), J1.66 (H1-14), J1.69 (H2-17), J1.73 (H2-21), J1.74 (H1-22), J1.81 (H2-29), J1.82 (H1-30), J1.84 (H1-32), J1.99 (H2-47), J1.100 (H2-48), J2.3, J2.4, J2.11, J3.3, R2.1, R4.2, R5.1, R26.2, S1.3, S1.4, SW1.1 (A), TP1.1, U1.12 (VSSA), U1.18 (VSS_4), U1.31 (VSS_1), U1.47 (VSS_2), U1.63 (VSS_3), U2.1 (GND), U3.1 (GND), U4.4 (GND), U5.12 (GND), U6.3, U6.5, U6.10, U6.11, U6.12, U7.3, U7.5, U7.10, U7.11, U7.12, U8.3, U8.5, U8.10, U8.11, U8.12, U9.3, U9.5, U9.10, U9.11, U9.12, U10.2, U10.4, U10.6, U11.2, U11.4, U11.6, U12.2, U12.4, U12.6, U13.2, U13.4, U13.6, U14.9 (AD0/SDO), U14.18 (GND), U14.20 (GND), U15.18 (GND), U15.20 (GND), U16.4 (VSS), U16.9 (Sink), Y1.2, Y1.4; also elsewhere on the board
I2C1_SCL: J1.43 (H1-43), J2.5, U1.58 (PB6/I2C1_SCL/TIM4_CH1/USART1_TX)
I2C1_SDA: J1.41 (H1-41), J2.6, U1.59 (PB7/I2C1_SDA/FSMC_NADV/TIM4_CH2/USART1_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)
IMU_SCL_1V8: Q2.2 (S), R24.1, U14.23 (SCL/SCLK), U15.23 (SCL/SCLK)
IMU_SCL_3V3: Q2.3 (D), R25.1, U1.29 (PB10/I2C2_SCL/USART3_TX/TIM2_CH3)
IMU_SDA_1V8: Q1.2 (S), R10.1, U14.24 (SDA/SDI), U15.24 (SDA/SDI)
IMU_SDA_3V3: Q1.3 (D), R11.1, U1.30 (PB11/2C2_SDA/USART3_RX/TIM2_CH4)
MuxEnable: U1.10 (PC2/ADC123_IN12), U5.15 (~E)
MuxOut: U1.17 (PA3/USART2_RX/TIM5_CH4/ADC123_IN3/TIM2_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), U4.1, U4.2
MuxOut_1: R3.1, U5.1 (COM_I/O)
MuxS0: U1.11 (PC3/ADC123_IN13), U5.10 (S0)
MuxS1: U1.14 (PA0-WKUP/USART2_CTS/ADC123_IN0/TIM2_CH1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), U5.11 (S1)
MuxS2: U1.15 (PA1/USART2_RTS/ADC123_IN1/TIM5_CH2/TIM2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), U5.14 (S2)
MuxS3: U1.16 (PA2/USART2_TX/TIM5_CH3/ADC123_IN2/TIM2_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), U5.13 (S3)
unnamed: C10.1, U1.6 (PD1-OSC_OUT/FSMC_D3/CAN_TX), Y1.1
unnamed: C13.1, U1.5 (PD0-OSC_IN/FSMC_D2/CAN_RX), Y1.3
unnamed: C18.1, R6.1, U5.9 (I0), U6.1
unnamed: C19.1, R7.2, U5.8 (I1), U6.7
unnamed: C20.1, R8.1, U5.7 (I2), U6.14
unnamed: C21.2, R9.2, U5.6 (I3), U6.8
unnamed: C25.1, R12.1, U5.19 (I12), U7.1
unnamed: C26.1, R13.2, U5.18 (I13), U7.7
unnamed: C27.1, R14.1, U5.23 (I8), U8.1
unnamed: C28.1, R15.2, U5.22 (I9), U8.7
unnamed: C29.1, R16.1, U5.5 (I4), U9.1
unnamed: C30.1, R17.2, U5.4 (I5), U9.7
unnamed: C31.1, R18.1, U5.17 (I14), U7.14
unnamed: C32.2, R19.2, U5.16 (I15), U7.8
unnamed: C33.1, R20.1, U5.21 (I10), U8.14
unnamed: C34.2, R21.2, U5.20 (I11), U8.8
unnamed: C35.1, R22.1, U5.3 (I6), U9.14
unnamed: C36.2, R23.2, U5.2 (I7), U9.8
unnamed: C41.1, U14.10 (REGOUT)
unnamed: C42.1, U15.10 (REGOUT)
unnamed: C43.1, FB2.2, U16.8 (VDD)
unnamed: D1.1 (K), R2.2
unnamed: D2.1 (K), R5.2
unnamed: D3.1 (K), R26.1
unnamed: R3.2, R4.1, U4.3
PD1_O1: C18.2, R6.2, U6.2, U11.1
PD1_O2: C29.2, R16.2, U9.2, U10.1
PD1_O3: C27.2, R14.2, U8.2, U12.1
PD1_O4: C25.2, R12.2, U7.2, U13.1
PD2_O1: C19.2, R7.1, U6.6, U11.3
PD2_O2: C30.2, R17.1, U9.6, U10.3
PD2_O3: C28.2, R15.1, U8.6, U12.3
PD2_O4: C26.2, R13.1, U7.6, U13.3
PD3_O1: C20.2, R8.2, U6.13, U11.5
PD3_O2: C35.2, R22.2, U9.13, U10.5
PD3_O3: C33.2, R20.2, U8.13, U12.5
PD3_O4: C31.2, R18.2, U7.13, U13.5
PD4_O1: C21.1, R9.1, U6.9, U11.7
PD4_O2: C36.1, R23.1, U9.9, U10.7
PD4_O3: C34.1, R21.1, U8.9, U12.7
PD4_O4: C32.1, R19.1, U7.9, U13.7
SYS_JTCK-SWCLK: J3.2, U1.49 (PA14/JTCKSWCLK)
SYS_JTMS-SWDIO: J3.1, U1.46 (PA13/JTMSSWDIO)

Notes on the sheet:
PMOD Test Connector
Test Points
IMU Circuitry
1V8 I2C Pullups
Sun Sensor Mux Control
3V3 Power Generation
Sun Sensor Connectors
Sun Sensor Circuitry
MRAM Persistant Storage
PC104 Bus Connector
LED_3V3_CATHODE
SWD / Programming Header
1V8 Power Generation
M3 Mounting Holes
MCU - STM32F103RET6

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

Board: 4 copper layers, 90.2 x 95.9 mm, 108 parts (0 on the bottom side), 102 nets.

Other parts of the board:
SW2: TL3305CF260QG; SW_TL3305CF260QG

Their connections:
/NRST: SW2.1, SW2.2; also elsewhere on the board
GND: SW2.3, SW2.4; also elsewhere on the board

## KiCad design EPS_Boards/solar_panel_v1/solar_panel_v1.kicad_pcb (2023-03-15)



Board: 2 copper layers, 83.0 x 113.0 mm, 43 parts (2 on the bottom side), 27 nets.

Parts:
D1, D2, D3, D4, D5: D_Photo; DIO_SFH_2430-Z
D6: D_Temp; SOIC127P600X175-8N
H1, H2, H3, H4: MountingHole; MountingHole_2.2mm_M2_DIN965_Pad
J1, J2, J3, J4, J5, J6: Conn_01x01; PinHeader_1x01_P2.54mm_Vertical
J7: DF13-7P-1.25DS(20); Hirose_DF13-07P-1.25DS_1x07_P1.25mm_Horizontal
J8: DF-13-5P-1.25DS; Hirose_DF13-05P-1.25DS_1x05_P1.25mm_Horizontal
R1: 0; R_0603_1608Metric
SC1, SC2, SC3, SC4, SC5, SC6, SC7, SC8, SC9, SC10, SC11, SC12, SC13, SC14, SC15, SC16, SC17, SC18, SC19, SC20, SC21, SC22, SC23, SC24: Solar_Cell; TrisolX_Solar_Cell

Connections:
ADSC_PD_1: D1.1 (K), J2.1
ADSC_PD_2: D2.1 (K), J4.1
ADSC_PD_3: D3.1 (K), J6.1
ARRAY_PWR: J8.1, SC1.1 (+), SC5.1 (+), SC9.1 (+), SC13.1 (+), SC17.1 (+), SC21.1 (+)
ARRAY_RTN: J8.2, SC4.2 (-), SC8.2 (-), SC12.2 (-), SC16.2 (-), SC20.2 (-), SC24.2 (-)
EPS_PD_1: D5.1 (K), J8.5
EPS_TMP_1: J8.3, R1.2
GND: D1.2 (A), D2.2 (A), D3.2 (A), D4.2 (A), D5.2 (A), D6.4, J1.1, J3.2, J5.1, J7.2, J7.4, J7.6, J8.4
unnamed: D6.8, R1.1
unnamed: SC1.2 (-), SC2.1 (+)
unnamed: SC2.2 (-), SC3.1 (+)
unnamed: SC3.2 (-), SC4.1 (+)
unnamed: SC5.2 (-), SC6.1 (+)
unnamed: SC6.2 (-), SC7.1 (+)
unnamed: SC7.2 (-), SC8.1 (+)
unnamed: SC9.2 (-), SC10.1 (+)
unnamed: SC10.2 (-), SC11.1 (+)
unnamed: SC11.2 (-), SC12.1 (+)
unnamed: SC13.2 (-), SC14.1 (+)
unnamed: SC14.2 (-), SC15.1 (+)
unnamed: SC15.2 (-), SC16.1 (+)
unnamed: SC17.2 (-), SC18.1 (+)
unnamed: SC18.2 (-), SC19.1 (+)
unnamed: SC19.2 (-), SC20.1 (+)
unnamed: SC21.2 (-), SC22.1 (+)
unnamed: SC22.2 (-), SC23.1 (+)
unnamed: SC23.2 (-), SC24.1 (+)

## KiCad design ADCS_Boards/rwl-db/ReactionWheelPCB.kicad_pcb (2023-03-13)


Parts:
C1, C2, C3, C4, C6, C8, C10, C12: 10nF; C_0603_1608Metric
H1, H2, H3, H4: MountingHole_Pad; MountingHole_3.2mm_M3_Pad_TopBottom
J1: PC104_Connector; pc104-connector
J2, J3, J4, J5: Conn_02x11_Odd_Even; 1-1734248-1-reaction-wheel-connector
R1, R2, R3, R4: 10k; R_0603_1608Metric
R5, R7, R9, R11: 5k; R_0603_1608Metric
R6, R8, R10, R12: 1M; R_0603_1608Metric
U1: Controller 1; Escon24.2
U2: Controller 2; Escon24.2
U3: Controller 3; Escon24.2
U4: Controller 4; Escon24.2
U5, U6: LM358N; DIP794W45P254L959H508Q8

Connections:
+5V: J1.65 (H2-13), U5.8 (V+), U6.8 (V+)
+12V: J1.60 (H2-8), U1.4, U2.4, U3.4, U4.4
Direction(S1): J1.20 (H1-20), U1.16
Direction(S2): J1.21 (H1-21), U2.16
Direction(S3): J1.22 (H1-22), U3.16
Direction(S4): J1.23 (H1-23), U4.16
Enable(S1): J1.16 (H1-16), U1.14
Enable(S2): J1.17 (H1-17), U2.14
Enable(S3): J1.18 (H1-18), U3.14
Enable(S4): J1.19 (H1-19), U4.14
GND: C1.1, C2.1, C3.1, C4.1, C6.1, C8.1, C10.1, C12.1, J1.61 (H2-9), J1.66 (H2-14), J1.69 (H2-17), J1.73 (H2-21), J1.74 (H2-22), J1.81 (H2-29), J1.82 (H2-30), J2.9, J2.10, J3.9, J3.10, J4.9, J4.10, J5.9, J5.10, U1.5, U1.18, U1.21, U1.23, U2.5, U2.18, U2.21, U2.23, U3.5, U3.18, U3.21, U3.23, U4.5, U4.18, U4.21, U4.23, U5.4 (GND), U6.4 (GND)
unnamed: C6.2, R5.1, R6.2
unnamed: C8.2, R7.2, R8.1
unnamed: C10.2, R9.1, R10.2
unnamed: C12.2, R11.2, R12.1
unnamed: R5.2, U5.1, U5.2
unnamed: R7.1, U5.6, U5.7
unnamed: R9.2, U6.1, U6.2
unnamed: R11.1, U6.6, U6.7
unnamed: J2.19, J2.20, J2.21, J2.22, U1.1
unnamed: J2.15, J2.16, J2.17, J2.18, U1.2
unnamed: J2.11, J2.12, J2.13, J2.14, U1.3
unnamed: J2.1, J2.2, U1.6
unnamed: J2.5, J2.6, U1.7
unnamed: J2.7, J2.8, U1.8
unnamed: J2.3, J2.4, U1.9
unnamed: J3.19, J3.20, J3.21, J3.22, U2.1
unnamed: J3.15, J3.16, J3.17, J3.18, U2.2
unnamed: J3.11, J3.12, J3.13, J3.14, U2.3
unnamed: J3.1, J3.2, U2.6
unnamed: J3.5, J3.6, U2.7
unnamed: J3.7, J3.8, U2.8
unnamed: J3.3, J3.4, U2.9
unnamed: J4.19, J4.20, J4.21, J4.22, U3.1
unnamed: J4.15, J4.16, J4.17, J4.18, U3.2
unnamed: J4.11, J4.12, J4.13, J4.14, U3.3
unnamed: J4.1, J4.2, U3.6
unnamed: J4.5, J4.6, U3.7
unnamed: J4.7, J4.8, U3.8
unnamed: J4.3, J4.4, U3.9
unnamed: J5.19, J5.20, J5.21, J5.22, U4.1
unnamed: J5.15, J5.16, J5.17, J5.18, U4.2
unnamed: J5.11, J5.12, J5.13, J5.14, U4.3
unnamed: J5.1, J5.2, U4.6
unnamed: J5.5, J5.6, U4.7
unnamed: J5.7, J5.8, U4.8
unnamed: J5.3, J5.4, U4.9
PWM-SetValue(S1): J1.24 (H1-24), U1.17
PWM-SetValue(S2): J1.25 (H1-25), U2.17
PWM-SetValue(S3): J1.26 (H1-26), U3.17
PWM-SetValue(S4): J1.27 (H1-27), U4.17
RampControl(S1)_IN: J1.37 (H1-37), R1.1
RampControl(S1)_Out: R6.1, U1.24
RampControl(S1)_RC: C1.2, R1.2, U5.3
RampControl(S2)_IN: J1.38 (H1-38), R2.1
RampControl(S2)_Out: R8.2, U2.24
RampControl(S2)_RC: C2.2, R2.2, U5.5
RampControl(S3)_IN: J1.39 (H1-39), R3.1
RampControl(S3)_Out: R10.1, U3.24
RampControl(S3)_RC: C3.2, R3.2, U6.3
RampControl(S4)_IN: J1.40 (H1-40), R4.1
RampControl(S4)_Out: R12.2, U4.24
RampControl(S4)_RC: C4.2, R4.2, U6.5

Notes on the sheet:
Motor Controllers and Motor Connectors (S3/S4)
M3 Mounting Holes
Unity Buffers (S3/S4)
Motor Controllers and Motor Connectors (S1/S2)
PC104 Bus Connector
Ramp Control PWM to DC Filters
Unity Buffers (S1/S2)


Board: 4 copper layers, 90.2 x 95.9 mm, 36 parts (0 on the bottom side), 63 nets.

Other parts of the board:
Brachiosaurus: LOGO

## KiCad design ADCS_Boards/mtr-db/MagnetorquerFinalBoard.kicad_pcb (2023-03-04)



Board: 4 copper layers, 90.2 x 95.9 mm, 59 parts (5 on the bottom side), 40 nets.

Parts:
C1, C3, C4, C5, C7, C9, C10, C11, C12: 0.1u; C_0603_1608Metric
C2, C6, C8: 10u; C_0603_1608Metric
D1, D2, D3, D4: ORANGE; LED_0603_1608Metric
H1, H2, H3, H4: MountingHole_Pad; MountingHole_3.2mm_M3_Pad_TopBottom
H5, H6, H7, H8: MountingHole_Pad; MountingHole_2.2mm_M2_Pad_TopBottom
J1: PC104_Connector; pc104-connector
JP1, JP2, JP3, JP4: SolderJumper_2_Open; SolderJumper-2_P1.3mm_Open_TrianglePad1.0x1.5mm
QXF1, QXF2: IRLR120N; TO-252-2
QXR1, QXR2: IRLR120N; TO-252-2
QYF1, QYF2: IRLR120N; TO-252-2
QYR1, QYR2: IRLR120N; TO-252-2
QZF1, QZF2: IRLR120N; TO-252-2
QZR1, QZR2: IRLR120N; TO-252-2
R1, R2, R3: 100k; R_0603_1608Metric
R4, R5, R6, R7: 2k2; R_0603_1608Metric
U1: X/Y_Coils; Front Coils Mount
U2: Z_Coil; ZCoil
UDX1: SN74LVC1G18DBVR; SOT95P280X145-6N
UDY1: SN74LVC1G18DBVR; SOT95P280X145-6N
UDZ1: SN74LVC1G18DBVR; SOT95P280X145-6N
ULX1: MIC29302WU; TO-263-5_TabPin3
ULY1: MIC29302WU; TO-263-5_TabPin3
ULZ1: MIC29302WU; TO-263-5_TabPin3
UPX1: MCP42010; SOIC127P600X175-14N
UPY1: MCP42010; SOIC127P600X175-14N
UPZ1: MCP42010; SOIC127P600X175-14N

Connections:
5V: C1.1, C3.1, C4.1, C5.1, C7.1, C9.1, C10.1, C11.1, C12.1, D1.2 (A), J1.77 (H2-25), J1.78 (H1-26), UDX1.5 (VCC), UDY1.5 (VCC), UDZ1.5 (VCC), ULX1.2 (VIN), ULY1.2 (VIN), ULZ1.2 (VIN), UPX1.14 (VDD), UPY1.14 (VDD), UPZ1.14 (VDD)
Enable: J1.42 (H1-42), UDX1.3 (A), UDY1.3 (A), UDZ1.3 (A), ULX1.1 (EN), ULY1.1 (EN), ULZ1.1 (EN)
GND: C1.2, C2.2, C3.2, C4.2, C5.2, C6.2, C7.2, C8.2, C9.2, C10.2, C11.2, C12.2, J1.61 (H2-9), J1.66 (H1-14), J1.69 (H2-17), J1.73 (H2-21), J1.74 (H1-22), J1.81 (H2-29), J1.82 (H1-30), J1.84 (H1-32), J1.99 (H2-47), J1.100 (H2-48), JP1.1 (A), JP2.1 (A), JP3.1 (A), JP4.1 (A), QXF2.3, QXR2.3, QYF2.3, QYR2.3, QZF2.3, QZR2.3, R1.1, R2.1, R3.1, UDX1.2 (GND), UDY1.2 (GND), UDZ1.2 (GND), ULX1.3 (GND), ULY1.3 (GND), ULZ1.3 (GND), UPX1.4 (VSS), UPY1.4 (VSS), UPZ1.4 (VSS)
unnamed: D1.1 (K), R4.1
unnamed: D2.1 (K), R5.1
unnamed: D3.1 (K), R6.1
unnamed: D4.1 (K), R7.1
unnamed: JP1.2 (B), R4.2
unnamed: JP3.2 (B), R5.2
unnamed: JP2.2 (B), R6.2
unnamed: JP4.2 (B), R7.2
SCK: J1.51 (H1-51), UPX1.2 (SCK), UPY1.2 (SCK), UPZ1.2 (SCK)
SPI: J1.52 (H1-52), UPX1.3 (SI)
SS: J1.50 (H1-50), UPX1.1 (~CS), UPY1.1 (~CS), UPZ1.1 (~CS)
X_COIL_A: QXF1.3, QXR2.2, U1.1 (X_Coil_A)
X_COIL_B: QXF2.2, QXR1.3, U1.2 (X_Coil_B)
X_FWD: QXF1.1, QXF2.1, UDX1.4 (Y1)
X_REV: QXR1.1, QXR2.1, UDX1.6 (Y2)
X_S: J1.44 (H1-44), UDX1.1 (S)
X_SO: UPX1.13 (SO), UPZ1.3 (SI)
X_VADJ: R2.2, ULX1.5 (ADJ), UPX1.5 (PB1), UPX1.6 (PW1), UPX1.9 (PW0), UPX1.10 (PB0)
X_VCOIL: C6.1, D2.2 (A), QXF1.2, QXR1.2, ULX1.4 (VOUT), UPX1.7 (PA1)
X_VCON: J1.47 (H1-47), UPX1.8 (PA0)
Y_COIL_A: QYF1.3, QYR2.2, U1.3 (Y_Coil_A)
Y_COIL_B: QYF2.2, QYR1.3, U1.4 (Y_Coil_B)
Y_FWD: QYF1.1, QYF2.1, UDY1.4 (Y1)
Y_REV: QYR1.1, QYR2.1, UDY1.6 (Y2)
Y_S: J1.45 (H1-45), UDY1.1 (S)
Y_VADJ: R3.2, ULY1.5 (ADJ), UPY1.5 (PB1), UPY1.6 (PW1), UPY1.9 (PW0), UPY1.10 (PB0)
Y_VCOIL: C8.1, D4.2 (A), QYF1.2, QYR1.2, ULY1.4 (VOUT), UPY1.7 (PA1)
Y_VCON: J1.48 (H1-48), UPY1.8 (PA0)
Z_COIL_A: QZF1.3, QZR2.2, U2.1 (Z_COIL_A)
Z_COIL_B: QZF2.2, QZR1.3, U2.2 (Z_COIL_B)
Z_FWD: QZF1.1, QZF2.1, UDZ1.4 (Y1)
Z_REV: QZR1.1, QZR2.1, UDZ1.6 (Y2)
Z_S: J1.46 (H1-46), UDZ1.1 (S)
Z_SO: UPY1.3 (SI), UPZ1.13 (SO)
Z_VADJ: R1.2, ULZ1.5 (ADJ), UPZ1.5 (PB1), UPZ1.6 (PW1), UPZ1.9 (PW0), UPZ1.10 (PB0)
Z_VCOIL: C2.1, D3.2 (A), QZF1.2, QZR1.2, ULZ1.4 (VOUT), UPZ1.7 (PA1)
Z_VCON: J1.49 (H1-49), UPZ1.8 (PA0)

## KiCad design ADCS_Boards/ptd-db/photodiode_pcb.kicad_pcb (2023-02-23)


Board: 2 copper layers, 16.5 x 5.1 mm, 3 parts (0 on the bottom side), 2 nets.

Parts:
A: Conn_01x01; PinHeader_1x01_P2.54mm_Vertical
C: Conn_01x01; PinHeader_1x01_P2.54mm_Vertical
D1: SFH_2430-Z; DIO_SFH_2430-Z

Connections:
unnamed: A.1, D1.A
unnamed: C.1, D1.C

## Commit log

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2021-10-18 Set up OBC board for the 2021-2022 school year
    [STM32_Breakout.sch]
2021-10-26 Add boxes for each sub-project to add their circuitry.
    [STM32_Breakout.sch]
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2021-10-30 Add new microcontroller - STM32L4R5ZIT6P
    Old microcontroller is still there, just kept off to the left to review
    the pin definitions of the old one.
    [STM32_Breakout.sch]
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2021-11-15 Add new microcontroller that will be used. Add footprint and symbol for common resistors and capacitors Add VREF circuitry, VDDIO and VDDUSB circuit:wq
    [STM32_Breakout.sch]
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2021-11-22 Added power monitor circuit
    Still not sure if amp's footnote is updated
    [STM32_Breakout.sch]
2021-11-25 Added power monitor to circuit
    Added 8-pin max4372F (amplifies by 50 times) with corresponding footnote and current sensing resistor. Out voltage should have 0.3-3.0 V range
    [STM32_Breakout.kicad_pcb, STM32_Breakout.sch, max4372fesa_footprint_check.kicad_pcb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]
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2021-12-02 Fix symbol error on MRAM
    [STM32_Breakout.sch]
2021-12-02 Fix footprint issue with MRAM
    [STM32_Breakout.sch]
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2022-01-03 Add clock circuitry and power circuitry. Add footprints for devices that did not have any. Add ferrite beads as inputs to each power source for each circuit
    [STM32_Breakout.kicad_pcb, STM32_Breakout.sch, qsat5to3.3.sch]
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2022-01-14 Add many different circuit elements including connectors and some other passive elements
    [STM32_Breakout.kicad_pcb, STM32_Breakout.sch]
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2022-01-20 Made some final changes to the schematic. Create the location of each of the mounting holes as well as the location of key connectors.
    [STM32_Breakout.kicad_pcb, STM32_Breakout.sch]
2022-01-20 Extend length of MRAM pads so they are visible on the board Add bottom silk, paste and mask as they were not enabled
    [STM32_Breakout.kicad_pcb]
2022-01-21 Change location of board connectors to match ADCS board
    [STM32_Breakout.kicad_pcb]
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2022-01-24 Started tracing
    Added traces with J7 and J6 connectors to STM32. Connected power circuit.
    [STM32_Breakout.kicad_sch]
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2022-01-29 Added traces to the bottom of the board
    Added traces to card reader, clock and temperature sensor. Improved traces of J1. Still need to figure out trace widths of high voltage/current traces
    [STM32_Breakout.kicad_pcb, STM32_Breakout.kicad_sch]
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2022-02-08 Add all old footprints to new schematic Add usb input with usb-uart interfacing to provide manual commands using uart
    [STM32_Breakout-B_Cu.gbr, STM32_Breakout-Edge_Cuts.gbr, STM32_Breakout-F_Cu.gbr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]
2022-02-08 Minor changes to schematic to make it more readable
    [STM32_Breakout.kicad_sch]
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2022-02-11 Fix all clearance, silkscreen and trace errors. Partially fixed 3.3V traces
    [STM32_Breakout.kicad_pcb]
2022-02-11 Continue to work on power distribution within the board
    [STM32_Breakout.kicad_pcb, STM32_Breakout.kicad_sch]
2022-02-11 Fix all remaining errors and redesign power distribution on the board
    [STM32_Breakout.kicad_pcb, STM32_Breakout.kicad_sch]
2022-02-11 Fix one area of ground plane flooding
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2022-02-13 Completed final PCB layout changes. Added Gerber files and PDF versions of schematic and layout.
    ***********THIS IS OBC VERSION 1 FINAL*************
    [STM32_Breakout-B_Cu.gbr, STM32_Breakout-B_Mask.gbr, STM32_Breakout-B_Silkscreen.gbr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]
2022-02-28 Add photos of physical pcb front and backside
    [STM32_Breakout.kicad_sch]
2022-07-27 templates: pc104: include initial support for base template
    [payload-test.kicad_pcb, payload-test.kicad_sch, pc104-template.kicad_pcb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]
2022-07-29 templates: pc104: complete template with MH, PC104, and edges
    [payload-test.kicad_pcb, payload-test.kicad_sch, pc104-template.kicad_pcb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]
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2022-11-10 Added MCP3008 to convert current monitor analog to serial for pi
    [pc104-template.kicad_pcb, pc104-template.kicad_sch]
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2022-11-11 templates: pc104: include cutouts on all 4 edges
    [pc104-template.kicad_pcb, pc104-template.kicad_sch]
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2022-11-12 Fixed libraries path for current monitor in OBC DB
    [pc104-template.kicad_pcb]
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2022-11-14 obc: daughterboard: clean up all schematics for easier reworks
    [current_monitor_sch.kicad_sch, pc104-template.kicad_pcb, pc104-template.kicad_sch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]
2022-11-14 footprint fix
    [current_monitor_sch.kicad_sch, pc104-template.kicad_pcb, pc104-template.kicad_sch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]
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2022-11-22 add buzzer footprint
    [fullsat.kicad_pcb]
2022-11-23 Added most wirings, such as pc104 to raspberry, i2c , RTC, temp sensor
    Still need to figure out if our power circuit works before wiring
    [pc104-template.kicad_pcb]
2022-11-23 Replaced mcp3008 footprint to smd chip
    [current_monitor_sch.kicad_sch, pc104-template.kicad_pcb, pc104-template.kicad_sch]
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2022-12-06 Updated RW and MCU PCBS. Layouts are complete, just need to do routing. (Pushed for Yasin Shahrami)
    [MC_SunSensorPCB.kicad_sch, ReactionWheelPCB.kicad_pcb, ReactionWheelPCB.kicad_sch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]
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2022-12-17 initial routing done ~ fix bug still
    [comm-rfb.kicad_pcb, comm-rfb.kicad_sch]
2022-12-17 made PA smaller, added some missing GND connections, and connect AMP-ENABLE
    [comm-rfb.kicad_pcb]
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2022-12-18 template: pc104: change hole size and fix pin labels
    [pc104-template.kicad_sch]
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2022-12-28 comm-rfb: include correct spacing for cc1120-em connectors, remove traces
    [comm-rfb.kicad_pcb, comm-rfb.kicad_sch, rffrontend.kicad_sch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]
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2023-01-03 COMM: move comm-rfb and old transceiver board to have same directory structure
    [BOMV1_Feb_2019.xlsx, Link_budget.xlsx, NewBoard.ods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]
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2023-02-24 adcs: mtr-db: fixed back of PCB and updated silkscreen
    [MagnetorquerFinalBoard.kicad_pcb]
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2023-03-13 adcs: Updated rw-db with latest PWM filter design and added misc silkscreen
    [ReactionWheelPCB.kicad_pcb, ReactionWheelPCB.kicad_sch]
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2023-03-15 adcs: adcs-ctl: change all footprints to standard kicad footprints or qset footprints
    [MC_SunSensorPCB.kicad_sch]
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2023-03-15 adcs: adcs-ctl: updated MRAM chip to use correct footprint, minor routing and silkscreen changes.
    [MC_SunSensorPCB.kicad_pcb]
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2023-04-13 templates: pc104: remove material around MH locations, include step file for header connector
    [pc104-template.kicad_pcb, pc104-template.kicad_sch]
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2023-04-13 fixed burn wire connections
2023-04-13 updated burn wire connection
    [antenna-db.kicad_sch]
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2023-04-13 made pcb for sc4215 - used sc4216 pad since has same dimensions
    [sc4215-test-circuit.kicad_pcb, sc4215-test-circuit.kicad_sch]
2023-04-13 made pcb for adp7159 - used adp7158 footprint since had same dimensions
    [adp7159-test-circuit.kicad_pcb, adp7159-test-circuit.kicad_sch]
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2023-05-04 eps: battery board: fixed errors
    [VI_monitor.kicad_sch, cell_level_protection.kicad_sch]
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2023-05-04 eps: battery board: added AND gate for power control and cleaned up global labels
    [VI_monitor.kicad_sch, battery_board_v2.kicad_sch, cell_level_protection.kicad_sch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]
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

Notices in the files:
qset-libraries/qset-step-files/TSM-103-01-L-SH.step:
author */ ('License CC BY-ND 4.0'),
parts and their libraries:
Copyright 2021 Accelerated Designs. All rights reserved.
